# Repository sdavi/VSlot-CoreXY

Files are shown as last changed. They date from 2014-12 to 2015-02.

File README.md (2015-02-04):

CoreXY 3D Printer
==================

A V-Slot 3D printer using the CoreXY configuration. This printer uses V-Slot Wheels to provide linear motion in the X and Y axes.

Thanks to Zelogik's great [AluXY](https://github.com/zelogik/AluXY) 3D printer that this printer is based on, and jand1122's [RepRap-XY](https://github.com/jand1122/RepRap-XY) plastic version of the AluXY.

Frame Size: 400mm x 400mm x 500mm

Build Area (X x Y x Z): 210mm x 195mm x 240mm.  

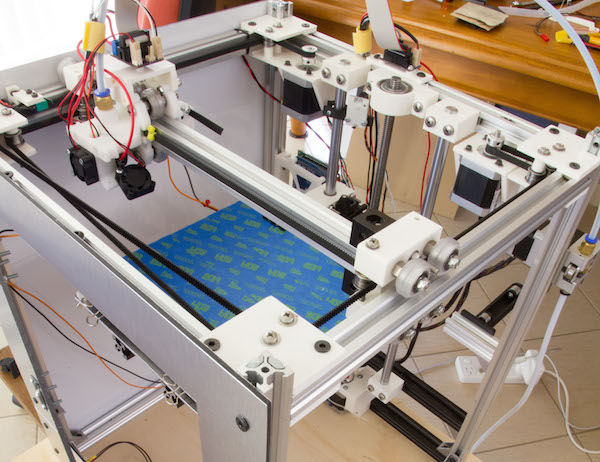
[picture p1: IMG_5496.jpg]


Assembly instructions can be downloaded here: [Assembly.pdf](Assembly/Assembly.pdf)

Updated BoM available here: [BoM.pdf](BoM.pdf)   *Note: This list is only a rough guide and there may be some inconsistencies due to various changes over time.*

All source code is written using OpenSCAD.

**Notice: This is a work in progress. Use at your own risk! **

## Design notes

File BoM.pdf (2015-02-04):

Qty | Description

20x20

v-‐slot

| aluminium extrusions

and

Accessories
4 | 500mm length V-‐Slot Extrusion
11 | 360mm length V-‐Slot Extrusion
1 | 310mm length V-‐slot Extrusion
8 | Hidden 90deg bracket
13 | 90 Degree Angle Corner Connector
12 | Solid V-‐Slot Wheel Kits
8 | Eccentric Spacer

Nuts

and

Screws
78 | T-‐Nuts
4 | Double t-‐nut
?? | Some drop-‐in t-‐nuts for later
M3
6 | M3 Nut
8 | M3 Nyloc Nut
8 | M3 Washer
4 | M3 Wingnut
4 | M3x15mm screws
4 | M3x25mm screws
4 | M3x30mm Screws
2 | M3x35 Screws
M4
16 | M4x40mm screws
4 | M4x60mm screws
8 | M3x10mm screws
60 | M4 washers
12 | M4 nuts
M5
48 | M5x8mm screws
12 | M5x25mm screws
6 | M5x30mm screws
14 | M5x40mm screws
16 | M5x45mm screws
30 | M5 washers
10 | M5 nuts

Other
2 | 400mm length 12mm diameter smooth rod
2 | LM12LUU linear bearing
1 | 400mm TR10x2 Trapezoidal leadscrew
1 | 10X2 flanged trapezoidal bronze nut
1 | 5mmx10mm coupler
1 | 6300Z bearing

3 | NEMA17

Stepper

motor

24 | F624ZZ flanged bearings
| Approx. 3-‐4m GT2 belt
2 | 20 tooth GT2 Pulley
1 | RAMPS/other electronics
1 | Power Supply
1 | 214x214mm Heat Bed PCB
1 | 225x225mm Aluminium 3mm sheet
1 | J-‐Head Hotend
1 | ReprapDiscount Bulldog XL Extruder
1 | ReprapDiscount Hall Endstop
2 | Mechanical Microswitch
1 | 200x212mm 3mm Borosilicate Glass
4 | Bulldog Clips
3 | 25mm 12V fan (1 for cooling jhead fins and 2 optional for part cooling)
| Screws to fit above fans

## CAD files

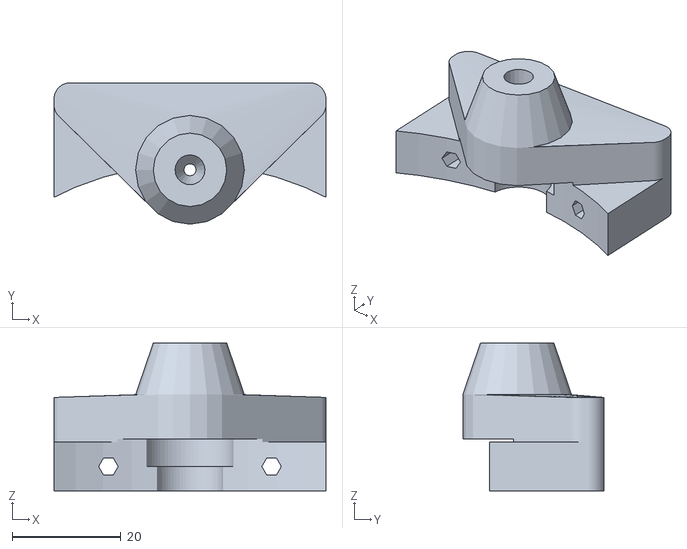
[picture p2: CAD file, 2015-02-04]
stl/hotend/jhead_bowden_hotend_mount_1.75_6mm.stl
50.0 x 26.0 x 27.2

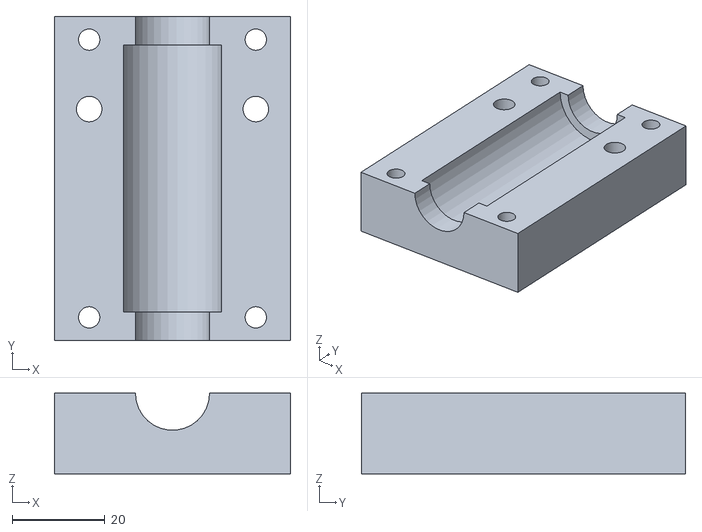
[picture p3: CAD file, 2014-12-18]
stl/z_carriage_outer.stl
51.0 x 70.0 x 17.4

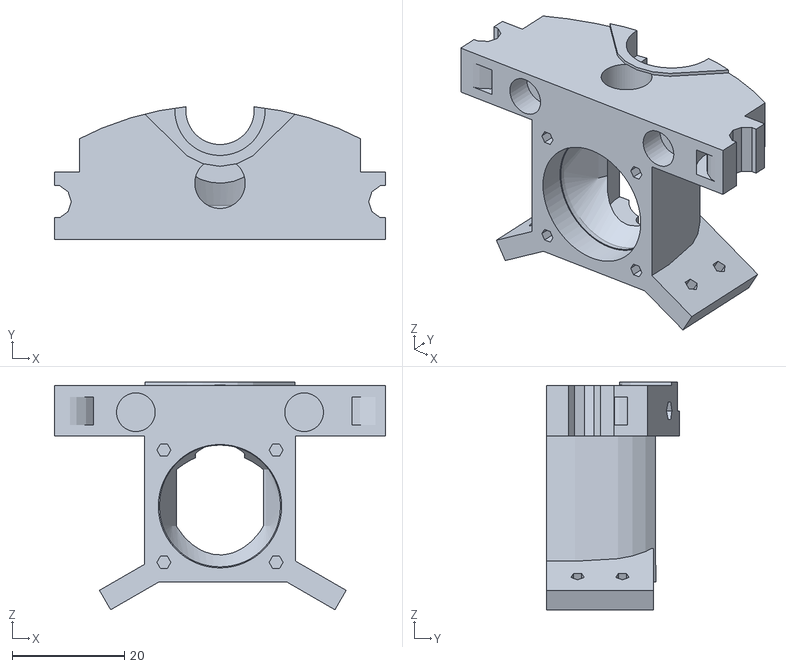
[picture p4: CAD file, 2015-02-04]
stl/hotend/jhead_bowden_hotend_mount_fan.stl
59.0 x 23.6 x 40.6

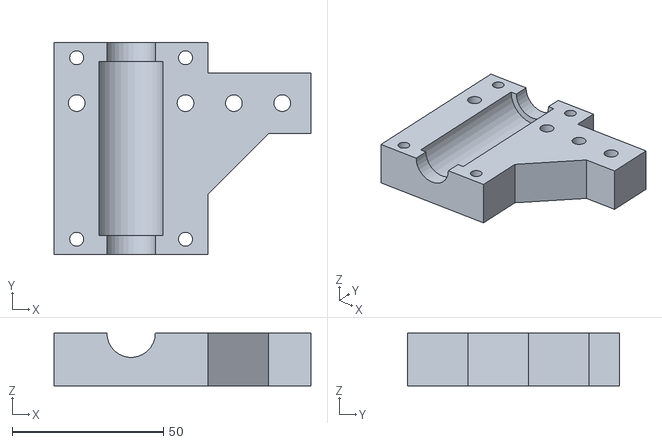
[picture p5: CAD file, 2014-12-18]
stl/z_carriage_inner.stl
85.0 x 70.0 x 17.4

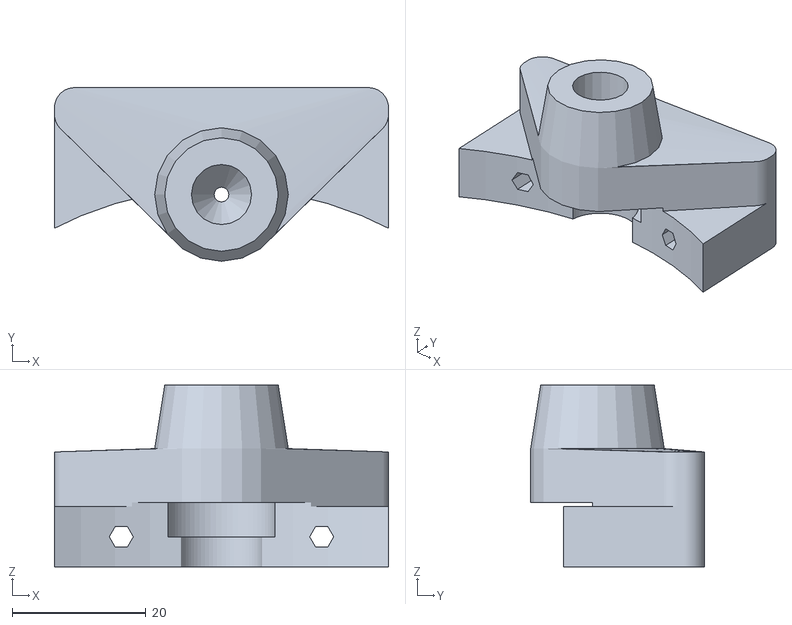
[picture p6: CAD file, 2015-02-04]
stl/hotend/jhead_bowden_hotend_mount_1.75_1_8bsp.stl
50.0 x 26.0 x 27.2

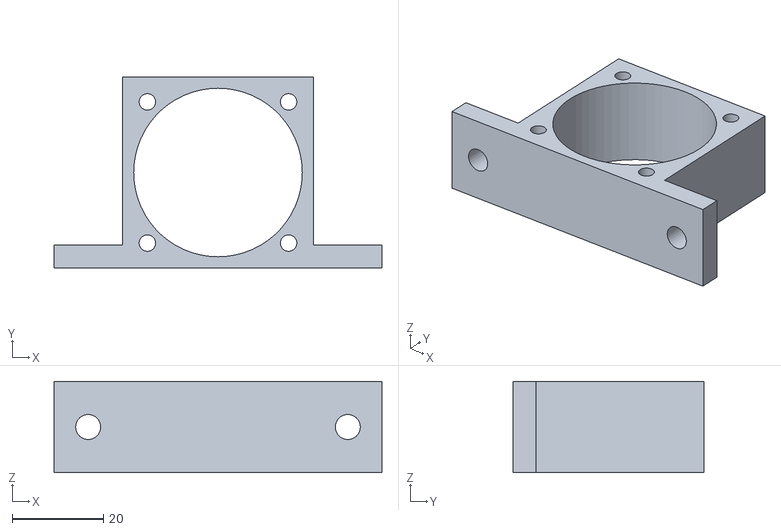
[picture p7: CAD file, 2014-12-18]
stl/bulldog_xl_mount.stl
72.0 x 42.0 x 20.0

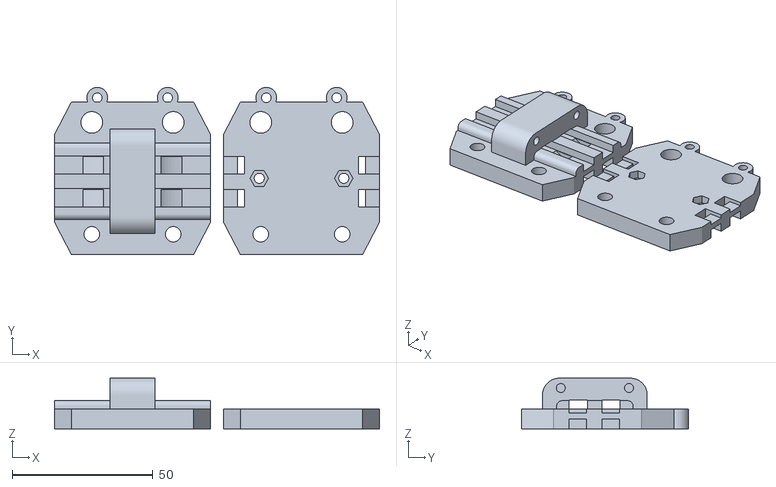
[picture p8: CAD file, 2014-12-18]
stl/x_carriage.stl
115.4 x 59.4 x 18.0

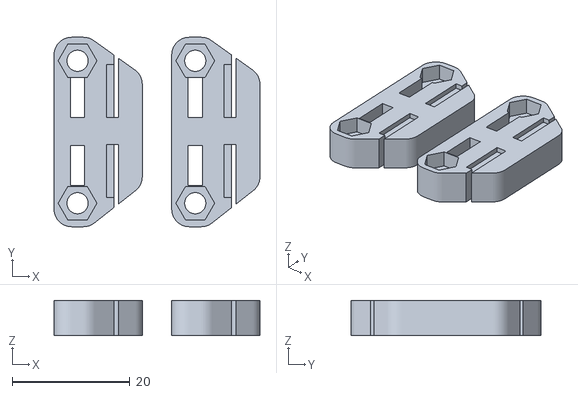
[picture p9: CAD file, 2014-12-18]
stl/x_carriage_tensioners.stl
35.0 x 32.2 x 6.00

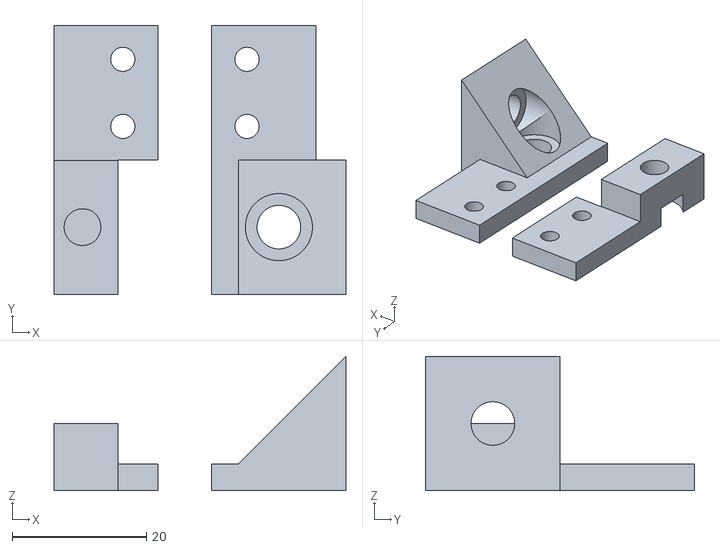
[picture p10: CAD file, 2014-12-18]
stl/endstop_holder.stl
43.5 x 40.0 x 20.0

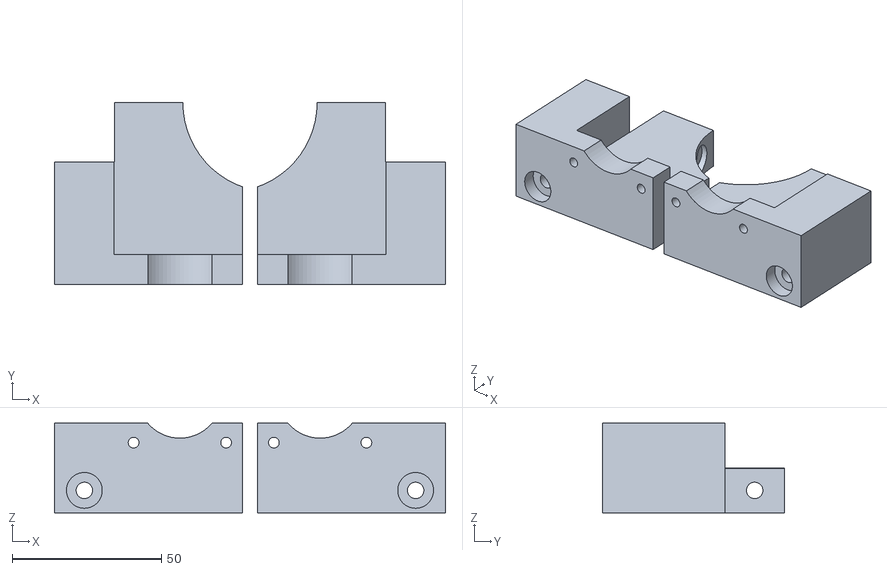
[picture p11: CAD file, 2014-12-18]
stl/z_motor_mount.stl
131.0 x 61.0 x 30.0

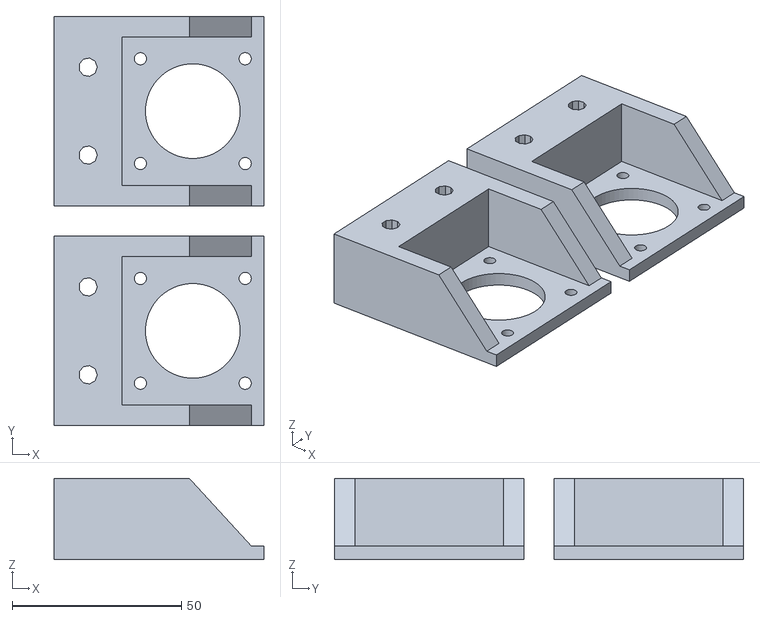
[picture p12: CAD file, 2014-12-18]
stl/y_motor_end.stl
62.0 x 121.0 x 24.0

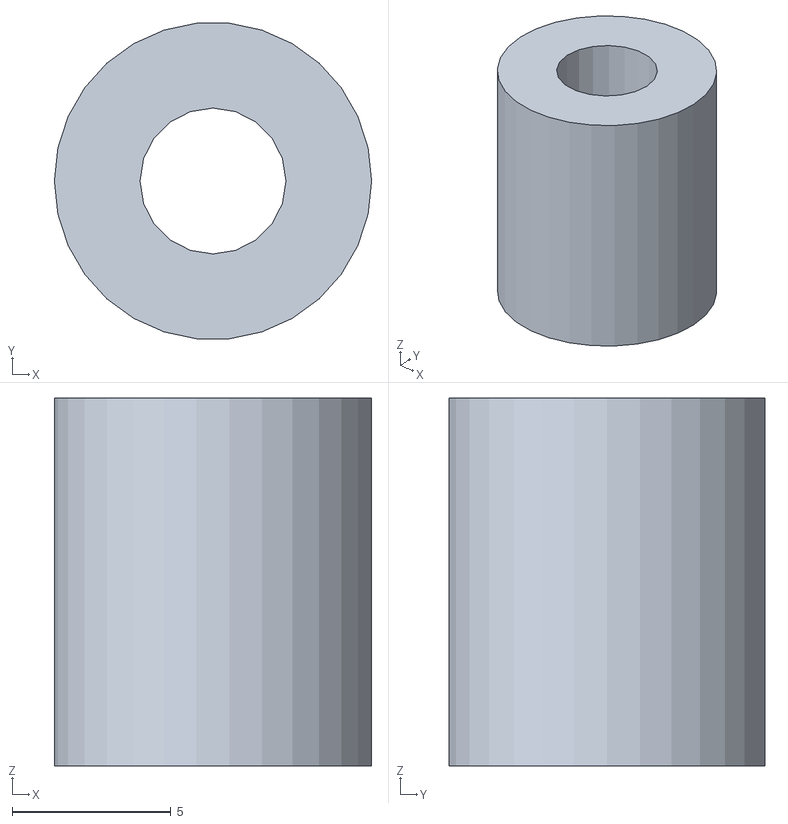
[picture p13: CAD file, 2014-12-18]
stl/belt_bearing_spacer.stl
10.0 x 9.95 x 11.6

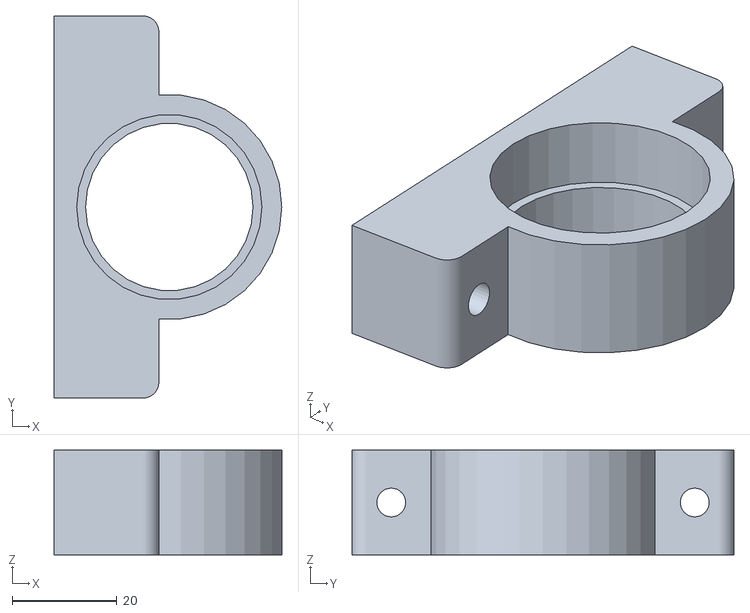
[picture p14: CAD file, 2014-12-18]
stl/z_bearing_mount.stl
43.5 x 73.0 x 20.0

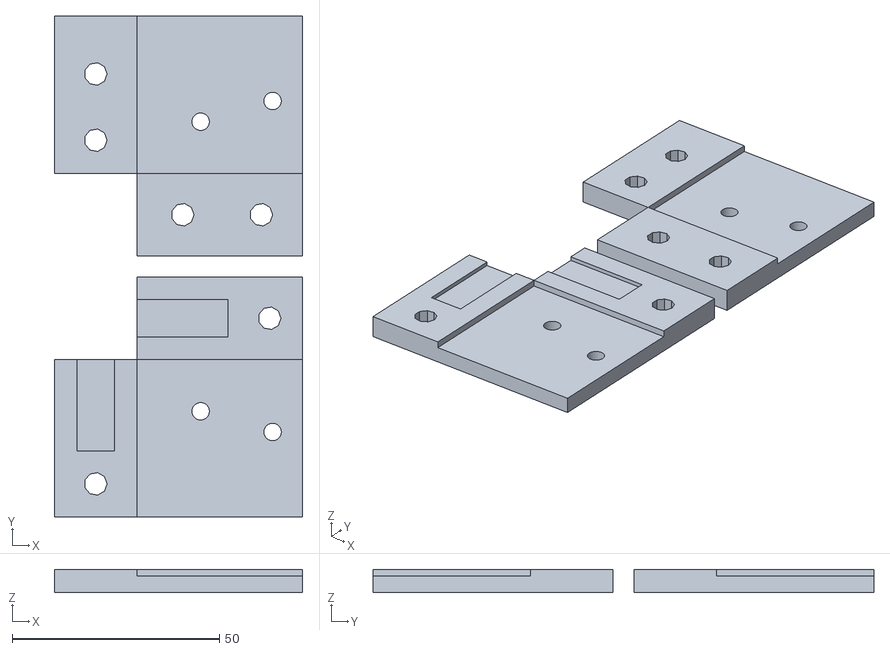
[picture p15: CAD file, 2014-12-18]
stl/y_idler_ends.stl
60.0 x 121.0 x 5.60

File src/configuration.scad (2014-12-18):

// Configuration
// Author: sdavi


include <dimensions.scad>
use <library.scad>


x_rod_distance = 45;

y_bearing = LM8UU;
x_bearing = LM8UU;
//z_bearing = LM12UUx2;
z_bearing = LM12LUU;
belt_bearing = BEARING_2x624;


end_belt_bearing_distance = 25;// distance between 2 bearings on y-ends
belt_clearance = 9.5; //space for belts
x_belt_clearance = 5; //spacing between x-axis vslot and belt

frame_screw = M5; //m5 screws for v/tslot

// calculated vars


//y bearing block
y_bearing_block_length = 2*y_bearing[2] + M3*2 + 5;
//y_bearing_block_width = y_bearing[1]+5;
y_bearing_block_width = 20; //vslot frame width

y_bearing_block_height = 6+y_bearing[1]/2;

//xy_bearing_distance = y_bearing_block_width/2+belt_clearance+belt_bearing[1]/2; //distance between center of y-bearing to center of x-belt bearing 
xy_bearing_distance = vslot_wheel[1]/2+vslot_wheel_spacer_length+belt_clearance+belt_bearing[1]/2; //distance between center of v_slot to center of x-belt bearing 




//min height for belt bearings
min_beltbearing_height = max(((belt_bearing[2]+m4_washer_thickness*2) * 2), y_bearing_block_height);

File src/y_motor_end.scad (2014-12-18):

// y_motor end spacer
// Author: sdavi


include <lib/y_motor_end.scad>

motor_mount();
translate([0,-65,0]) motor_mount();

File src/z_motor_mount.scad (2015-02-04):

// z_motor_mount
// Author: sdavi
// Based on jand1122's RepRap-XY: https://github.com/jand1122/RepRap-XY


include <lib/z_motor_mount.scad>


z_motor_end(single_piece=0);

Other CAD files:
stl/z_carriage_outer(mirror).stl
stl/hotend/jhead_bowden_hotend_mount_3.0_6mm.stl
stl/hotend/jhead_bowden_hotend_mount_3.0_1_8bsp.stl
stl/z_carriage_inner(mirror).stl
src/belt_bearing_spacer.scad
src/bulldog_xl_mount.scad
src/dimensions.scad
src/endstop_holder.scad
src/endstop_holder_rrd_halleffect.scad
src/hotend_mounts/E3D_bowden_hotend_mount.scad
src/hotend_mounts/jhead_bowden_hotend_mount.scad
src/hotend_mounts/jhead_dual_bowden_hotend_mount.scad
src/i3_adapters/i3_gregs_wades_mount.scad
src/i3_adapters/i3_y_carriage_adapter.scad
src/library.scad
src/vslot_corner_connector.scad
src/x-carriage.scad
src/x-carriage_tensioners.scad
src/xy_block.scad
src/y_idler_ends.scad
src/y_idler_ends_mirror.scad
src/z_bearing_mount.scad
src/z_carriage_inner(mirror).scad
src/z_carriage_inner.scad
src/z_carriage_outer(mirror).scad
src/z_carriage_outer.scad
src/z_nut_holder.scad
src/z_rod_clamps.scad
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

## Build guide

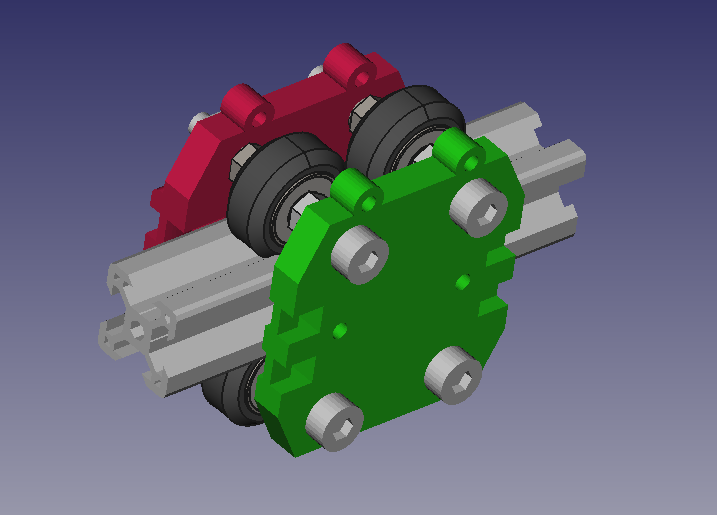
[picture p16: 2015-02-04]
Assembly/x-carriage-assembled1.png

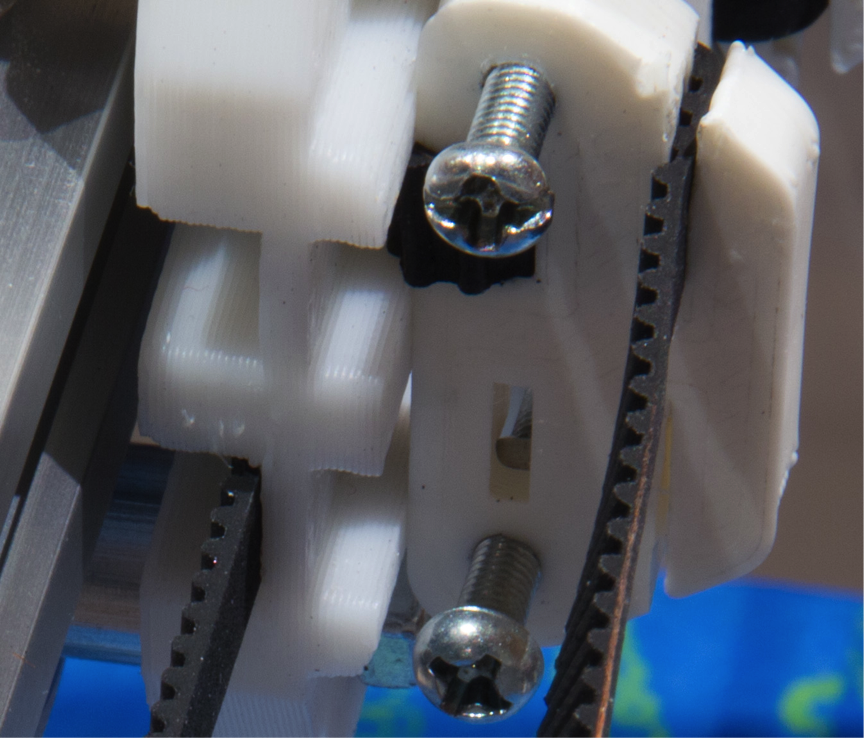
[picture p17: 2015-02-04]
Assembly/x-carriage_2.png

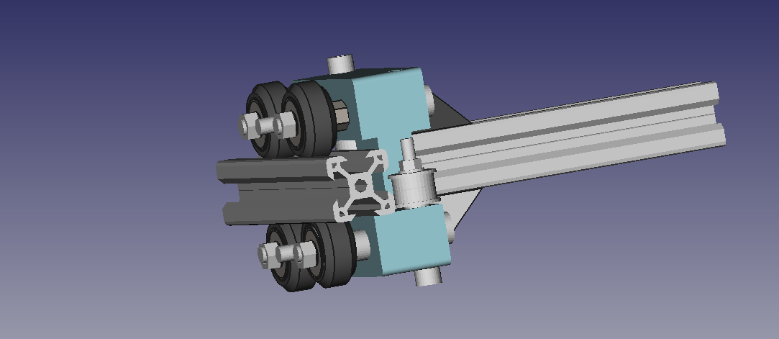
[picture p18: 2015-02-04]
Assembly/xy_block_assemble2.png

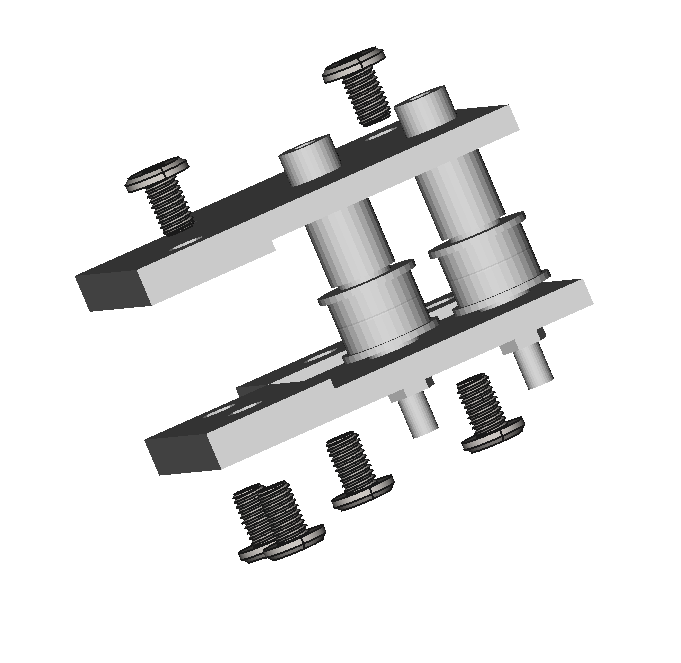
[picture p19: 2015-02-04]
Assembly/idler_end.png

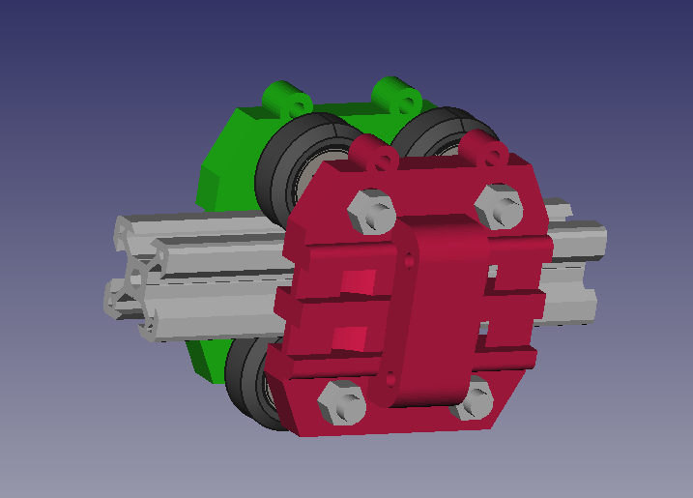
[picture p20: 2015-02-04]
Assembly/x-carriage-assembled2.png

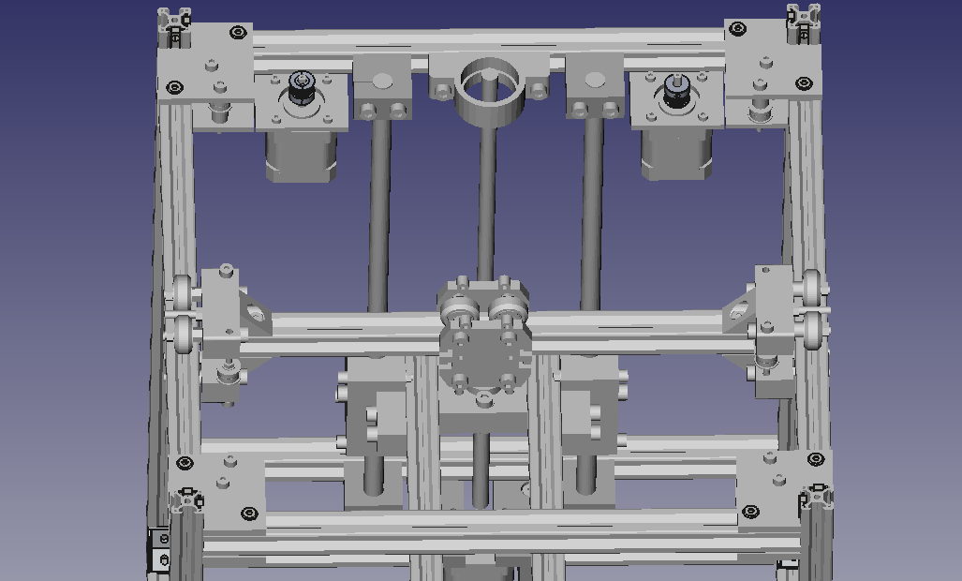
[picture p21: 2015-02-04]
Assembly/Frame4.png

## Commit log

2015-01-22 Updated BoM
    Updated BoM and swapped names of z_carriage_inner with z_carriage_outer.
    [jhead_dual_bowden_hotend_mount.scad, z_carriage_inner(mirror).scad, z_carriage_inner(mirror).stl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]
2015-02-04 Added Assembly Instruction and Updated BoM
    [jhead_bowden_hotend_mount.scad, jhead_bowden_hotend_mount_1.75_1_8bsp.stl, jhead_bowden_hotend_mount_1.75_6mm.stl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]
